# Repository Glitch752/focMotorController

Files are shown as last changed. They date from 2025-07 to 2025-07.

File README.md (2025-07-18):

# FOCMotorController

A 12v brushless DC motor controller capable of [field-oriented control](https://en.wikipedia.org/wiki/Vector_control_(motor)) (also known as vector control), which is a control system concept that can improve the efficiency and power output of motors using current-based feedback.

I wanted to learn how field-oriented control systems (and brushless motor controllers in general) work, so I made a PCB from scratch!

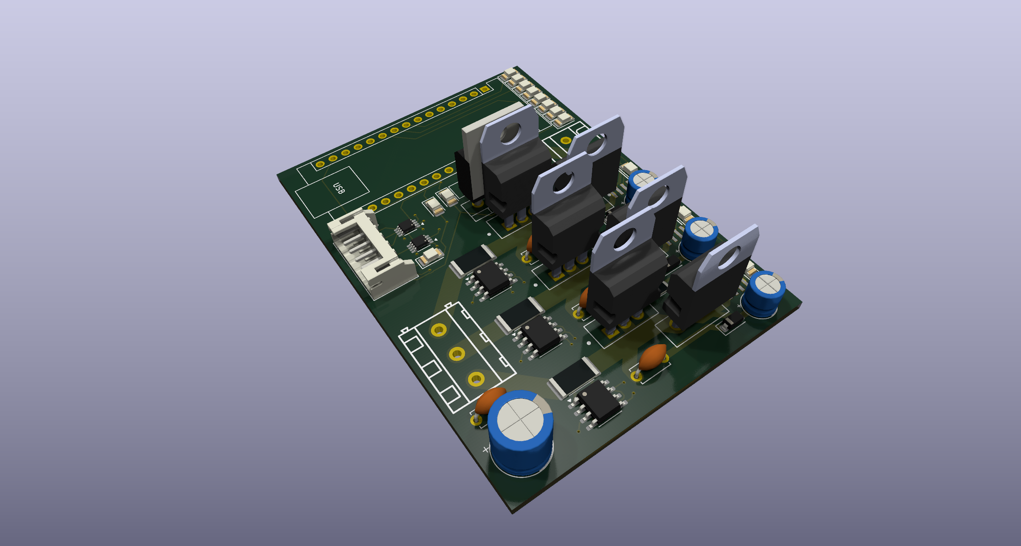
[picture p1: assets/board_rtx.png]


## Design goals
- Allow 30-amp continuous operation
- Run field-oriented control
- Runs off an RP2040 Arduino devboard
- Operate at relatively high efficiency: I don't have a specific goal in mind, but ideally it would experience less than a few watts loss at peak load
- Allow controlling the [REV NEO](https://www.revrobotics.com/rev-21-1650/) series motors from the FRC ecosystem because I have access to many old ones.
- Record accurate quadrature encoder readings for tight closed-loop control
- Build for under $200

## Bill of materials

There are a few main components I needed to choose for this project:
- **MOSFETs:** This is pretty much just a tradeoff between efficiency, size, and price. I landed on the STM [STP55NF06L](https://www.st.com/content/ccc/resource/technical/document/datasheet/49/c5/a8/71/93/60/4f/86/CD00002690.pdf/files/CD00002690.pdf/jcr:content/translations/en.CD000026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) power MOSFET,
which has a very low static resistance when on with a gate voltage of >10V. At only 3.3V, the resistance is quite high, meaning we need a gate driver circuit to improve the driver's efficiency.
- **Gate drivers**: I chose the [IR2104](https://www.infineon.com/dgdl/Infineon-IR2104-DS-v01_00-EN.pdf?fileId=5546d462533600a4015355c7c1c31671) half-bridge gate drivers primarily because they're cheap and widely available.
Also, since they're half-bridge, they manage both the voltage and ground MOSFETs for their phase, which simplifies the control logic.
- **Current measurement circuitry**: There are [quite a few methods available for sensing current](https://www.nxp.com/docs/en/application-note/AN14164.pdf) in motor controllers, but the simplest is using a shunt resistor and relying on Ohm's law.
This is what I ended up doing. I use a [INA240 amplifier](https://www.ti.com/lit/ds/symlink/ina240.pdf) reading across a 6mΩ resistor to convert the tiny voltage potential difference to something readable by the microcontroller.
I'm interested to see what the signal-to-noise ratio will look like.
- Other miscellaneous things like logic level shifters because we're using a 3.3v microcontroller and 5v encoders. All components use a relatively large form-factor where possible to make hand-soldering simpler (altough there are a few tiny SMT components).

Here are all the components required and their price as of July 2025 from JLCPCB.
Of course, many of these can be sourced cheaper elsewhere and soldered manually.

|Name |Purpose|Quantity|JLC part number|Total Price|
|---|---|---|---|---|
|STP55NF06L|The main MOSFET we use|6|[C77582](https://jlcpcb.com/partdetail/STMicroelectronics-STP55NF06L/C77582)|$5.91|
|IR2104STRPBF|The main gate drivers|3|[C2960](https://jlcpcb.com/partdetail/InfineonTechnologies-IR2104STRPBF/C2960)|$1.15|
|Arduino Nano RP2040 Connect|The microcontroller used|1|n/a|$19.10 (on Amazon)|
|SN74LVC2T45DCTR|Level shifters for quadrature encoder input|2|[C22672](https://jlcpcb.com/partdetail/TexasInstruments-SN74LVC2T45DCTR/C22672)|$0.44|
|INA240A1D|The amplifier used for current sensing|3|[C2060769](https://jlcpcb.com/partdetail/TexasInstruments-INA240A1D/C2060769)|$4.32|
|PA2512FKF7W0R006E|The low-resistance 6mΩ shunt resistor|3|[C728340](https://jlcpcb.com/partdetail/YAGEO-PA2512FKF7W0R006E/C728340)|$0.30|
|A16-1000|A resettable fuse for the power input|1|[C135398](https://jlcpcb.com/partdetail/Shenzhen_JDTFuse-A161000/C135398)|$0.09|
|KM477M035F16RR0VH2FP0|470uF capacitor for input smoothing|1|[C47888](https://jlcpcb.com/partdetail/48894-KM477M035F16RR0VH2FP0/C47888)|$0.05|
|KM477M035F16RR0VH2FP0|0.1uF capacitor for input smoothing|1|[C47888](https://jlcpcb.com/partdetail/48894-KM477M035F16RR0VH2FP0/C47888)|$0.05|
|50YXF1MEFC5X11|1uF capacitor for decoupling gate drivers|3|[C2927584](https://jlcpcb.com/partdetail/Rubycon-50YXF1MEFC5X11/C2927584)|$0.13|
|CC1H104MC1FD3F6C10SA|100nF capacitor for bootstrapping|3|[C5375966](https://jlcpcb.com/partdetail/Dersonic-CC1H104MC1FD3F6C10SA/C5375966)|$0.07|
|S6B-PH-K-S(LF)(SN)|6-pin JST connector for encoder|1|[C157920](https://jlcpcb.com/partdetail/JST-S6B_PH_K_S_LF_SN/C157920)|$0.07|
|XL-3216UGC-FB|Green status LEDs|3|[C3646937](https://jlcpcb.com/partdetail/XINGLIGHT-XL_3216UGCFB/C3646937)|$0.04|
|XL-3216SURC-FB|Red power LED|1|[C3646938](https://jlcpcb.com/partdetail/XINGLIGHT-XL_3216SURCFB/C3646938)|$0.01|
|B0530W|500mA diode for bootstrap power|3|[B0530W](https://jlcpcb.com/partdetail/2459-B0530W/C2102)|$0.10|
|MBR1045G|10A Schottky Diode for power source|1|[C79734](https://jlcpcb.com/partdetail/onsemi-MBR1045G/C79734)|$0.86|
|SMAJ15A|TVS diode for voltage spike protection|1|[C113958](https://jlcpcb.com/partdetail/115197-SMAJ15A/C113958)|$0.04|
|WJ128V-5.0-3P|Screw terminal block for phase output|1|[C8270](https://jlcpcb.com/partdetail/Ningbo_KangnexElec-WJ128V_5_03P/C8270)|$0.16|
|WJ128V-5.0-2P|Screw terminal block for voltage input|1|[C8269](https://jlcpcb.com/partdetail/Ningbo_KangnexElec-WJ128V_5_02P/C8269)|$0.11|
|1206W4J0332T5E|3.3kohm resistor, misc|1|[C26041](https://jlcpcb.com/partdetail/26784-1206W4J0332T5E/C26041)|$0.01|
|1206W4F2001T5E|2kohm resistor, misc|1|[C17944](https://jlcpcb.com/partdetail/18632-1206W4F2001T5E/C17944)|$0.01|
|1206W4J0621T5E|620ohm resistor, misc|1|[C25391](https://jlcpcb.com/partdetail/26134-1206W4J0621T5E/C25391)|$0.01|
|FRC1206J101 TS|100ohm resistor, misc|3|[C2907422](https://jlcpcb.com/partdetail/FOJAN-FRC1206J101TS/C2907422)|$0.01|
|1206W4F4702T5E|47kohm pulldown resistors|4|[C25833](https://jlcpcb.com/partdetail/26576-1206W4F4702T5E/C25833)|$0.02|
|FRC1206F19R6TS|19.6ohm gate resistors|6|[C2933621](https://jlcpcb.com/partdetail/FOJAN-FRC1206F19R6TS/C2933621)|$0.02|

Total part cost for 1 board:
- $8.02 without microcontroller or MOSFETs
- $13.93 without microcontroller
- $33.03 with microcontroller   

Note that, if you're doing assembly through something like JLCPCB, you'll need to make 5. If you don't need 5 boards, you can avoid assembly for the MOSFETs and order them yourself. They're one of the easiest components to solder on the board.

## FOC writeup
Here, I'll document my current knowledge of field oriented control for my own reference and to see what I need to look further into. Please note all this information may not be correct since BLDC control is still a new subject to me.

Field oriented control is a mechanism to control brushless DC motors that guarantees torque will always be applied directly perpendicular to the motor. It increases the efficiency, maximum speed, and power output of controlled motors. However, it's also relatively expensive to calculate and suffers from MOSFET switching losses because we must use PWM control to generate an effective sine wave.

### Definitions and acronyms
- **Motor**: A device that converts electrical energy into mechanical energy. Motors typically use moving permanent magnets and fixed electromagnets to generate a magnetic field that causes the rotor to spin.
  - **Winding**: A coil of wire that generates a magnetic field when current flows through it.
  - **Inductor**: Another name for a winding, typically used in the context of inductors that store energy in a magnetic field.
  - **Phase**: A set of windings in a motor that is independently controlled. Brushless motors typically have three phases, which are often referred to as A, B, and C or U, V, and W.
  - **Rotor**: The *rot*ating part of the motor containing permanent magnets. This is the part that spins.
    - **Poles**: The number of permanent magnets attached to the rotor. This isn't necessarily a multiple of the number of phases, but should be a multiple of 2 (since two identical magnet poles can't be beside each other).
  - **Stator**: The *stat*ionary part of the motor containing the windings. This is the part that generates the magnetic field. In a 3-phase motor, the stator has 3 sets of windings, each 120 electric degrees apart.
    - **Slots**: The number of coils on the stator. Motors will have a number of slots that is a multiple of the number of phases.
  - **BLDC**: Brushless DC. Brushed motors have physical contacts that dictate when phases are activated, while brushless motors rely on electrical signals to control the phases. Brushless motors can be faster, more reliable, and more efficient, but this comes at the cost of complexity.[<sup>1</sup>](#footnote-1)
  - **PMSM**: Permanent Magnet Synchronous Motors. The uses of this term are somewhat murky and confused with BLDC, so I will refrain from using it to avoid confusion.[<sup>2</sup>](#footnote-2)
  - **Mechanical angle**: The physical angle of the rotor in the motor; 1 revolution of the rotor is 360 degrees. The mechanical angle is used for position and speed feedback.
  - **Electrical angle**: The electrical angle describes the position of the rotor relative to the stator's magnetic field. It cycles faster than the mechanical angle by a factor equal to the number of pole pairs. The electrical angle is used for control calculations (e.g. it's the angle used in park and clarke transformations; see below).
- **FOC**: Field-oriented control, a method of controlling brushless motors that uses current-based feedback to apply torque directly perpendicular to the rotor.
- **Inverter**: Components that convert DC power to AC power. In our case, the circuitry that converts the motor controller's input voltage to phase voltages.
  - **MOSFET**: Metal-Oxide-Semiconductor Field-Effect Transistor; a particular type of transistor that can effectively act as a switch when appropriate signals are applied. 6 MOSFETs are used for BLDC motor control: one for ground and one for voltage of each phase.
  - **Gate driver / FET driver**: A circuit that controls MOSFETs, providing the necessary voltage while decoupling the microcontroller from the relatively high current draw of switching MOSFETs.
  - **Half bridge**: A circuit that controls two MOSFETs to switch a phase between voltage and ground. Half bridges are used for each phase in BLDC motor control.
- **Encoder**: A device that measures the position of the rotor relative to the stator. Accurate position measurement is crucial for FOC so we know where to apply torque.
  - **Hall effect sensor**: A type of sensor that detects magnetic fields.
  - **Quadrature encoder**: A type of encoder that uses two signals to determine the position of the rotor. It can detect both position and direction of rotation. Quadrature encoders can use hall sensors, optical sensors, or other methods.
    - **A/B channels**: Quadrature encoders have two primary outputs, A and B, which are 90 degrees out of phase. This communicates both velocity and direction of rotation.
    - **C channel / index**: Some quadrature encoders (including those we rely on) have a third channel, C, which indicates a specific position of the rotor. This is used for homing the rotor to find its initial position.
- **PWM**: Pulse-width modulation. A method of controlling the amount of power delivered by quicking switching something on and off.
  - **Duty cycle**: The percentage of time that a signal is on compared to the total time. For example, a 25% duty cycle means the signal is on for 25% of the time and off for 75% of the time.
  - **SVM**: Space vector modulation. An algorithm for effectively creating AC waveforms through PWM signals. SVM is commonly used for BLDC motor control because it reduces noise and vibration compared to more naive approaches.
- **Driving frequency**: Generally, the frequency of PWM pulses sent to the half bridge drivers. A higher driving frequency creates a smoother output signal but requires faster and more expensive hardware. Generally in the range of 20 to 80 kHz.
- **Control frequency**: The frequency of the control system driving the output voltages. Control systems generally operate around 1 to 5 kHz.
- **Inrunner/outrunner**: Two types of brushless motors that differ in how the stator and rotor are arranged.
  - **Inrunner**: The rotor is inside the stator, which typically contains large windings pointing inward. Inrunner motors generally have a higher maximum speed and efficiency.
  - **Outrunner**: The rotor is outside the stator, which typically contains smaller windings pointing outward. In some cases, this means the rotor is the outer body of the motor. In outrunner motors, the rotor is sometimes also called a can. Outrunner motors generally have a higher torque output.
- **Flux**: Shorthand for magnetic flux linkage. Magnetic flux linkage can be thought of as the "magnetic field strength" in the motor. For PMSM control, our reference flux is 0 (but we still need to control it to keep it there).
- There are many coordinate systems used for BLDC control; see [figure 1](#figure-1-a-diagram-of-coordinate-systems-used-in-foc). Here are the most important ones and their common names:
  - **Stator X axis / alpha**: The "horizontal" (on a side profile) axis of the motor stator.
  - **Stator Y axis / beta**: The "vertical" (on a side profile) axis of the motor stator.
  - **Winding U, V, and W axes**: The axes pointing outwards for the three phases of the motor, 120 degrees offset from each other. Axis U is typically aligned with the stator X axis.
  - **Rotor direct axis / d**: The axis of the rotor that is parallel to the rotor's magnetic field that generates flux.
  - **Rotor quadrature axis / q**: The axis of the rotor that is perpendicular to the rotor's magnetic field that generates torque.
- **Electromotive force / back EMF**: The voltage generated by the motor itself while spinning.[<sup>3</sup>](#footnote-3)
- Transformations are used in motor control to make manipulating the signals simpler.
  - **Clarke transformation**: Also known as the alpha-beta transformation; converts the three-phase stator currents u, v, and w into stator axes alpha and beta.
  - **Park transformation**: Also known as the direct-quadrature-zero transformation; converts stator-aligned components into rotor axes q and d with respect to the motor's rotating magnetic field.
- **Proportional-integral (PI) controller**: A feedback-based control mechanism to regulate processes that require dynamic adjustment or can't be precisely modelled mathematically. PI controllers are used to regulate rotor axis (q and d) currents by controlling the maximum PWM duty cycle for each phase.[<sup>4</sup>](#footnote-4)

### FOC process

The broad overview of FOC control is as follows:
1. Gather the measured position of the rotor using the encoder.
2. Transform phases into the rotor coordinate system.
3. Calculate the required current in the rotor quadrature axis (q) to generate the desired torque.
4. Calculate the required current in the rotor direct axis (d) to generate the desired magnetic field.
5. Transform the rotor coordinate system back to the phases' coordinate systems.
6. Calculate the required voltage to apply to each phase to generate the desired current.
7. Apply the calculated voltage to each phase using PWM.
8. Repeat at a high frequency.

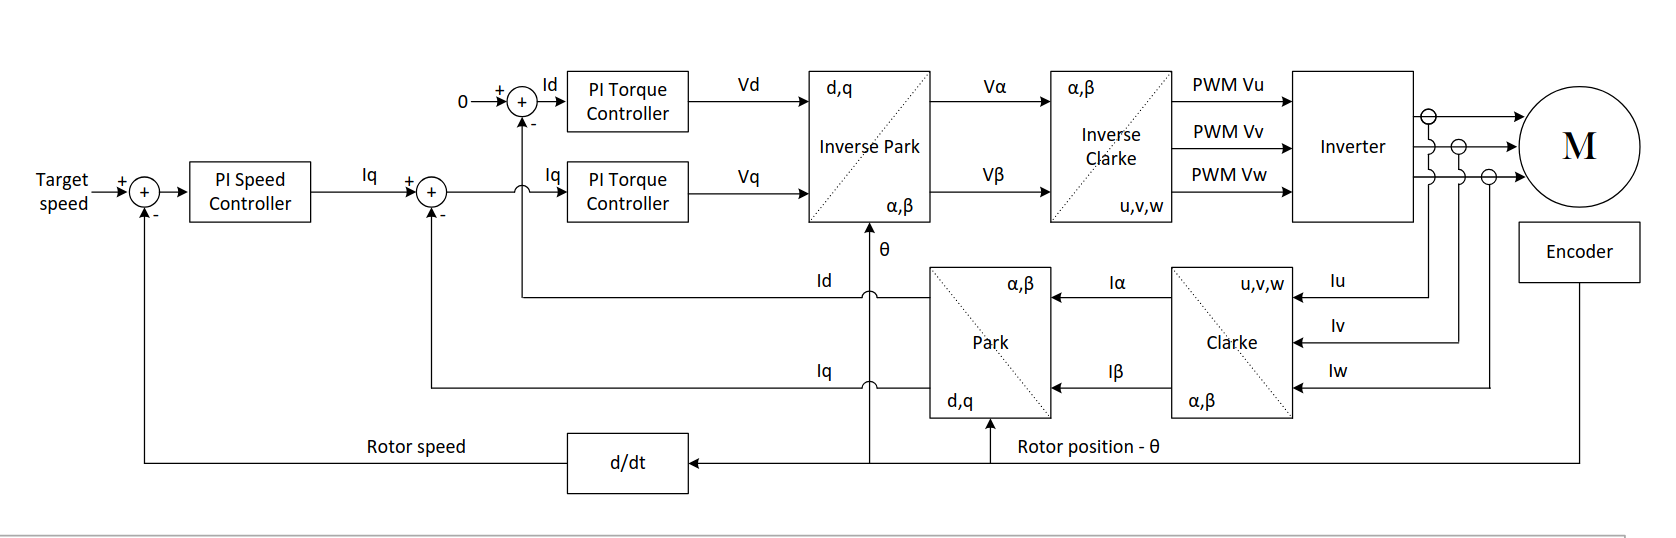
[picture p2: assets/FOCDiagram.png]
FOC diagram showing the above process

From [this great presentation](https://www.ti.com/lit/ml/slyp711/slyp711.pdf).  

There are a few important things to note:
- We can't track the encoder position fast enough to respond accurately to the rotor position at high speeds,
  so we must perform latency compensation of some sort.
- The current in the rotor direct axis (d) is typically set to zero, meaning we only control the rotor quadrature axis (q).
  This is because the d-axis current doesn't generate torque, so we don't care about it for most applications.
- This doesn't account for current limiting, which is a whole separate topic that I honestly
  don't understand very well. Currently, I naively clamp the applied current to a maximum value.

### Footnotes

<h4 id="footnote-1"><sup>1</sup> "Brushless DC"</h4>
Confusingly, "brushless DC motor control" is often used to refer to brushless motors that are controlled with DC voltage through a motor controller, even though the motor itself is an AC motor. This is because the motor controller generates a sine wave using PWM signals, which is then applied to the motor phases.

<h4 id="footnote-2"><sup>2</sup> "Permanent Magnet Synchronous Motors. The uses of this term are somewhat murky and confused with BLDC [...]"</h4>
Technically, brushless motors can also be switched reluctance motors or induction motors (also known as asynchronous motors). However, the majority of brushless DC motors are PMSM. Synchronous motors are a subset of brushless motors whose speed is independent of the load.

<h4 id="footnote-3"><sup>3</sup> "Back EMF is the voltage generated by the motor itself while spinning"</h4>
When brushless motors spin, the rotor generates current in the stator that opposes the applied voltage. Back EMF is linearly proportional to the rotational speed of the motor, so it's one of the forces that limits brushless motors' maximum speed.  
Back EMF is sometimes used to determine the position and speed of brushless motors in sensorless control, but almost never for FOC because it's not precise enough. It can also be used to our advantage for "braking", which entails shorting the phases together to make the motor resist rotation.  
  
<h4 id="footnote-4"><sup>4</sup> "PI controllers are a feedback-based control mechanism [...]"</h4>
PI controllers take the error between the current and desired state as an input and adjust the output based on the error. They have two components (hence the name): a proportional component that linearly adjusts the output based on the error, and an integral component that accumulates error over time. The two components are added to get the final output.  
PI controllers are a subset of the more general PID controllers, which also include a derivative component that predicts future error based on the rate of change of the error. In a PI controller, the components serve different purposes; the proportional component provides immediate response to error, while the integral component helps eliminate steady-state error by adjusting the output based on accumulated error over time.  

### Figures
#### Figure 1: A diagram of coordinate systems used in FOC
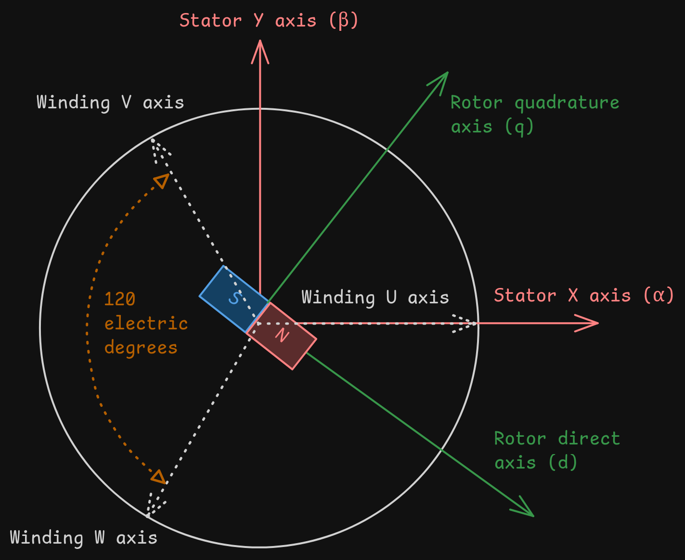
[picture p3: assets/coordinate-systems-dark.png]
A graphical explanation of stator, rotor, and winding motor coordinate systems


## Software
Currently, there's a testing piece of software written in Python to run on a local system and simulate the motor controller.
Obviously, Python won't be fast enough for high-speed closed-loop control on the motor controller,
so I'll move to C++ once I have the ability to test more easily.

## Hackatime
Project name: `focMotorController`



Note that I initially had some issues with kicad-wakatime, so it didn't track ~8 hours of work :(

## Future investigation (once I actually have a PCB lol)
- Does it actually work?
- Do we need a heatsink? We should be dissipating an average of ~0.32W per MOSFET at peak load, and 2 watts spread over 6 devices is a very minimal amount of heat. Maybe if we drive it harder, but the rest of the circuit would probably break before the MOSFETs...
- There's an interesting new-ish algorithm seen primarily in acadamia called [Deadbeat Direct Torque and Flux Control](https://www.mdpi.com/1996-1073/15/9/3009); how difficult would it be to implement this?
- Understand and determine the advantages of [discontinuous PWM](https://imperix.com/doc/implementation/discontinuous-pwm) signaling

### Future investigation for the PCB
- Should we have separate enable lines per half bridge?
- Is there a more efficient and accurate, yet inexpensive, way to measure current?
- How can I minimize signal noise in a board carrying high current?
- How can I improve the gate driver circuitry to minimize switching losses?
- Should we instead use full half bridge chips instead of drivers and MOSFETs?

## Resources
- [Current Sensing Techniques in Motor Control Applications - NXP](https://www.nxp.com/docs/en/application-note/AN14164.pdf)
- [Bootstrap Circuitry Selection for Half Bridge Configurations - Texas Instruments](https://www.ti.com/lit/an/slua887a/slua887a.pdf)
- [Bypass Capacitor, Its Functions and Applications - Elprocus](https://www.elprocus.com/bypass-capacitor-its-functions-and-applications/)
- [How to Make Advanced BLDC Motor Controllers - Altium](https://resources.altium.com/p/build-advanced-brushless-motor-controller)
- [Field-Oriented Control (FOC) for BLDC Motors: A Beginner’s Guide - Mechtex](https://mechtex.com/blog/field-oriented-control-foc-for-bldc-motors-a-beginners-guide)
- [Discontinuous PWM (DPWM) - Imperix](https://imperix.com/doc/implementation/discontinuous-pwm)
- [Proportional–integral–derivative controller](https://en.wikipedia.org/wiki/Proportional%E2%80%93integral%E2%80%93derivative_controller)
- [Space vector modulation - Wikipedia](https://en.wikipedia.org/wiki/Space_vector_modulation)
- [Space Vector PWM Intro - Switchcraft](https://www.switchcraft.org/learning/2017/3/15/space-vector-pwm-intro) (has great animations)
- [Protect Your BLDC Motor Drive with Cycle-by-cycle Current Limit Control - Texas Instruments](https://www.ti.com/lit/ta/ssztbp2/ssztbp2.pdf)
- [PMSM Control with DSCs and MCUs - Microchip](https://www.microchip.com/en-us/solutions/technologies/motor-control-and-drive/motor-types/permanent-magnet-synchronous-motors)
- [Vector control (motor) - Wikipedia](https://en.wikipedia.org/wiki/Vector_control_(motor))
- [Demystifying BLDC motor commutation - Texas Instruments](https://www.ti.com/lit/ml/slyp711/slyp711.pdf)
- [Alpha–beta transformation - Wikipedia](https://en.wikipedia.org/wiki/Alpha%E2%80%93beta_transformation)
- [Direct-quadrature-zero transformation - Wikipedia](https://en.wikipedia.org/wiki/Direct-quadrature-zero_transformation)
- [Field Oriented Control (FOC) - A Deep Dive - Performance Motion Devices](https://www.pmdcorp.com/resources/type/articles/get/field-oriented-control-foc-a-deep-dive-article)
- [fasaxc/pico-bldc - Github](https://github.com/fasaxc/pico-bldc/tree/main)

### Datasheets
- [INA240 Bidirectional, Ultra-Precise Current Sense Amplifier](https://www.ti.com/lit/ds/symlink/ina240.pdf)
- [Datasheet IR2104(S) & (PbF)](https://www.infineon.com/dgdl/Infineon-IR2104-DS-v01_00-EN.pdf?fileId=5546d462533600a4015355c7c1c31671)
- [Datasheet STP55NF06L N-channel Power MOSFET](https://www.st.com/content/ccc/resource/technical/document/datasheet/49/c5/a8/71/93/60/4f/86/CD00002690.pdf/files/CD00002690.pdf/jcr:content/translations/en.CD000026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)

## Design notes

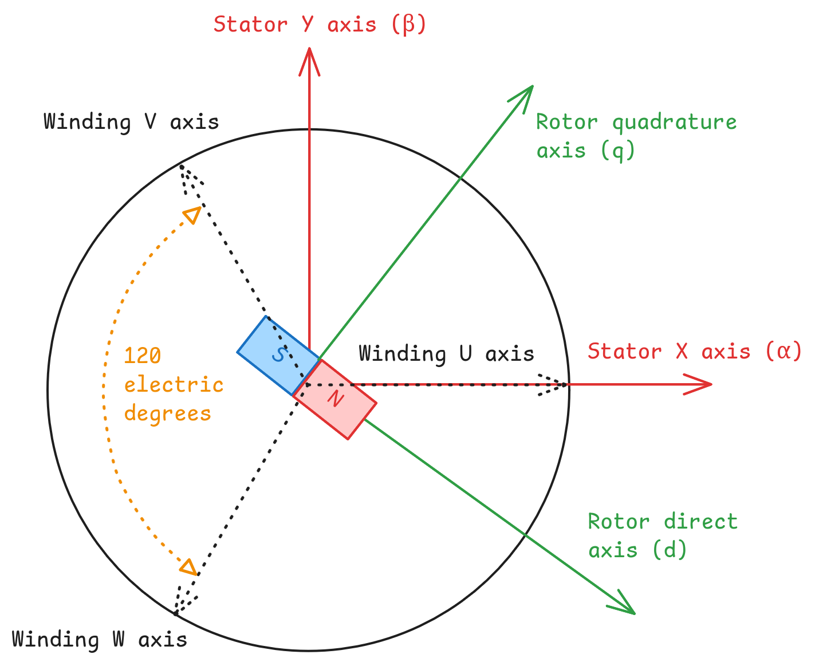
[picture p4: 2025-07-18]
assets/coordinate-systems.png

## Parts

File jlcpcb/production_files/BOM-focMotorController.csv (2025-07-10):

Comment | Designator | Footprint | LCSC | Quantity
SMAJ15A - TVS diode for voltage spike protection | D1 | D_SMA | C113958 | 1
Resettable polyfuse for overcurrent protection | F1 | A16-1000 | C135398 | 1
JST-PH encoder connection | J2 | JST_PH_S6B-PH-K_1x06_P2.00mm_Horizontal | C157920 | 1
2k | R2 | R_1206_3216Metric | C17944 | 1
Amplifier A | U12,U13,U14 | SOIC-8_3.9x4.9mm_P1.27mm | C2060769 | 3
Bootstrap charger | D7,D8,D9 | D_SOD-123 | C2102 | 3
74LVC2T45DC | U1,U2 | VSSOP-8_2.3x2mm_P0.5mm | C22672 | 2
620ohm | R3 | R_1206_3216Metric | C25391 | 1
Pulldown 47k | R11,R13,R7,R8 | R_1206_3216Metric | C25833 | 4
3.3k | R1 | R_1206_3216Metric | C26041 | 1
100ohm | R4,R5,R6 | R_1206_3216Metric | C2907422 | 3
Decoupling B 1uF/25V | C6,C7,C8 | CP_Radial_D5.0mm_P2.00mm | C2927584 | 3
Gate BL 19.6ohm | R10,R12,R19,R20,R22,R9 | R_1206_3216Metric | C2933621 | 6
IR2104 Gate Driver B | U10,U11,U9 | IR2104SPBF | C2960 | 3
Status LED 1 (green) | D4,D5,D6 | LED_1206_3216Metric | C3646937 | 3
Power LED (red) | D3 | LED_1206_3216Metric | C3646938 | 1
0.1uF ceramic | C2 | C_Disc_D5.0mm_W2.5mm_P5.00mm | C400087 | 1
470uF electrolytic | C1 | CP_Radial_D8.0mm_P3.50mm | C47888 | 1
Bootstrap A 0.1uF/25v | C3,C4,C5 | C_Disc_D5.0mm_W2.5mm_P5.00mm | C5375966 | 3
Shunt A 6uohm | R14,R15,R16 | R_2512_6332Metric | C728340 | 3
MOSFET A low | U3,U4,U5,U6,U7,U8 | STP55NF06L | C77582 | 6
MBR1045G | D2 | TO-220-2_Vertical | C79734 | 1
Power input | P2 | WJ128V-5.0-2P | C8269 | 1
WJ128V-5.0-3P | P1 | WJ128V-5.0-3P | C8270 | 1

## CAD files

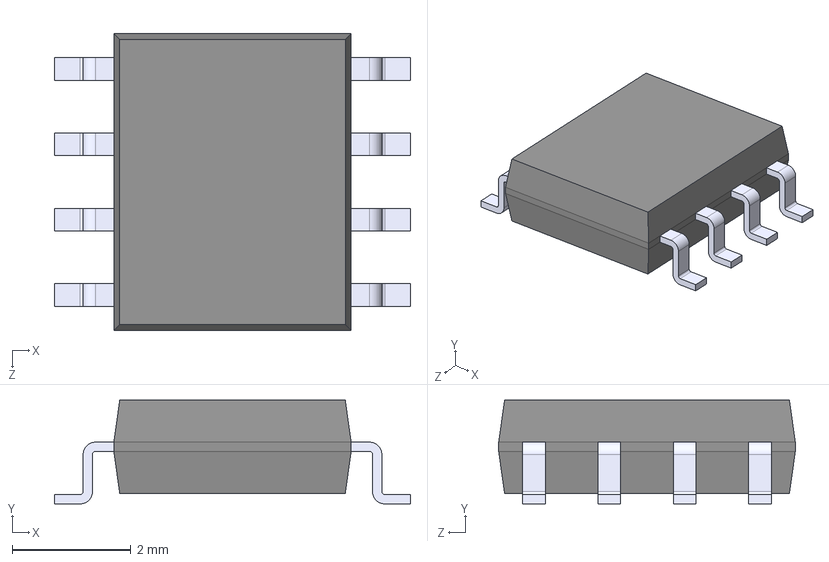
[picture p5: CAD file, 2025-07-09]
footprints/IR2104SPBF.step
6.00 x 1.75 x 5.00 mm

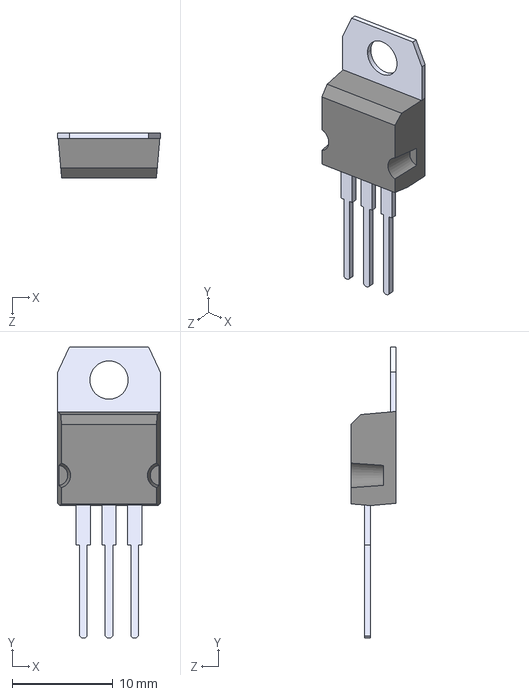
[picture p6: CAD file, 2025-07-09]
footprints/STP55NF06L.step
10.2 x 28.9 x 4.50 mm

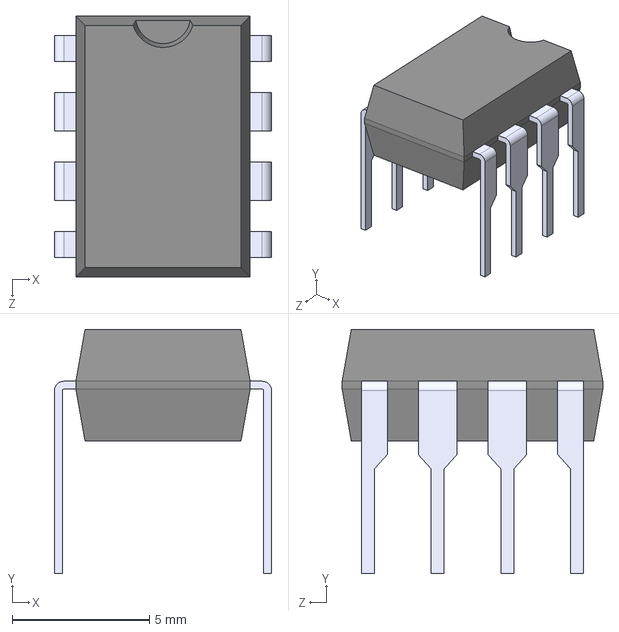
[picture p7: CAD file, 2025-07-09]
footprints/TC4420EPA.step
7.91 x 8.89 x 9.50 mm

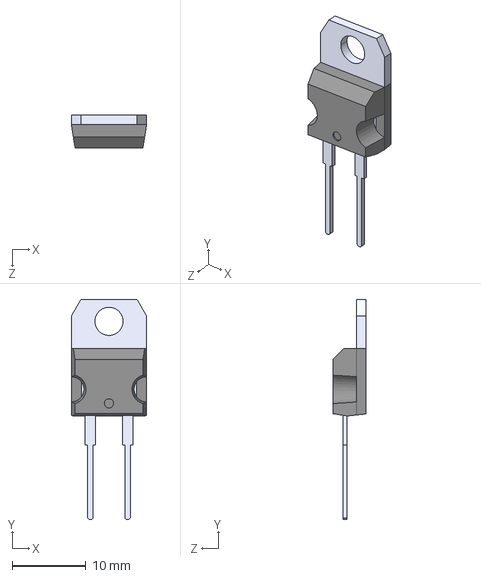
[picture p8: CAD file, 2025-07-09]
footprints/STPS20L15D.step
10.2 x 29.8 x 4.50 mm

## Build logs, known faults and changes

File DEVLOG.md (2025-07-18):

# Small devlog

Total time spent so far: ~19 hours (~11 tracked by hackatime)

## Initial research
Time taken: ~2 hours

I determined the appropriate MOSFETs and circuitry required for field-oriented control.

## Initial PCB
Time taken: ~8 hours

I made the schematic and PCB layout in KiCad for the bare-minimum driver circuitry required for FOC. There were a few flaws with my initial design, like measuring current on the low MOSFET source, which I learned isn't sufficient for field-oriented control.

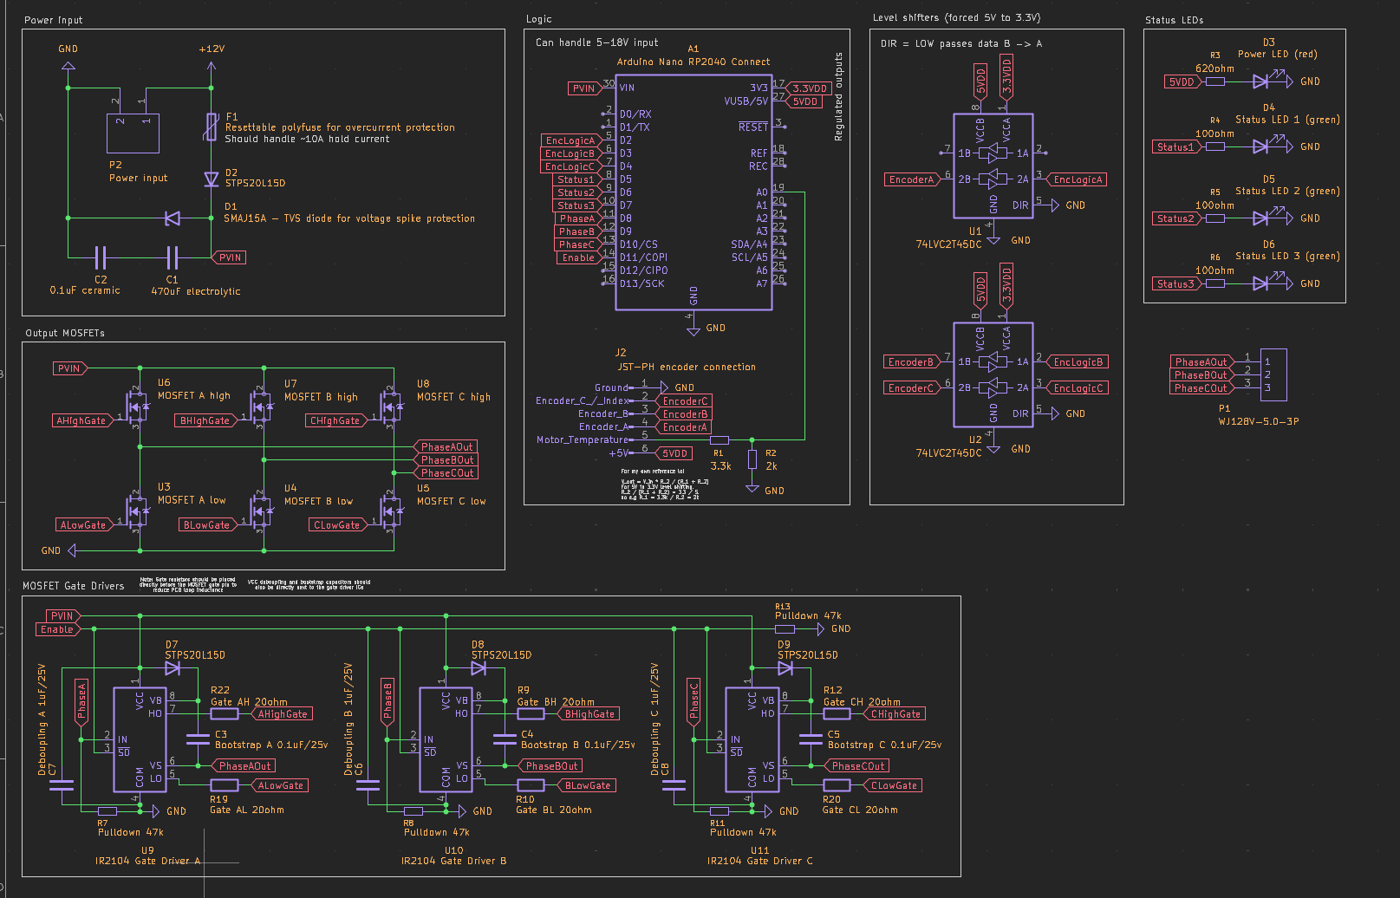
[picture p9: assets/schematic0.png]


## Iterating on the PCB
Time taken: ~3 hours

I iterated on the design to make the PCB much more compact and clean. I'm not yet aware of any issues with the new version of the PCB, so next up is software.

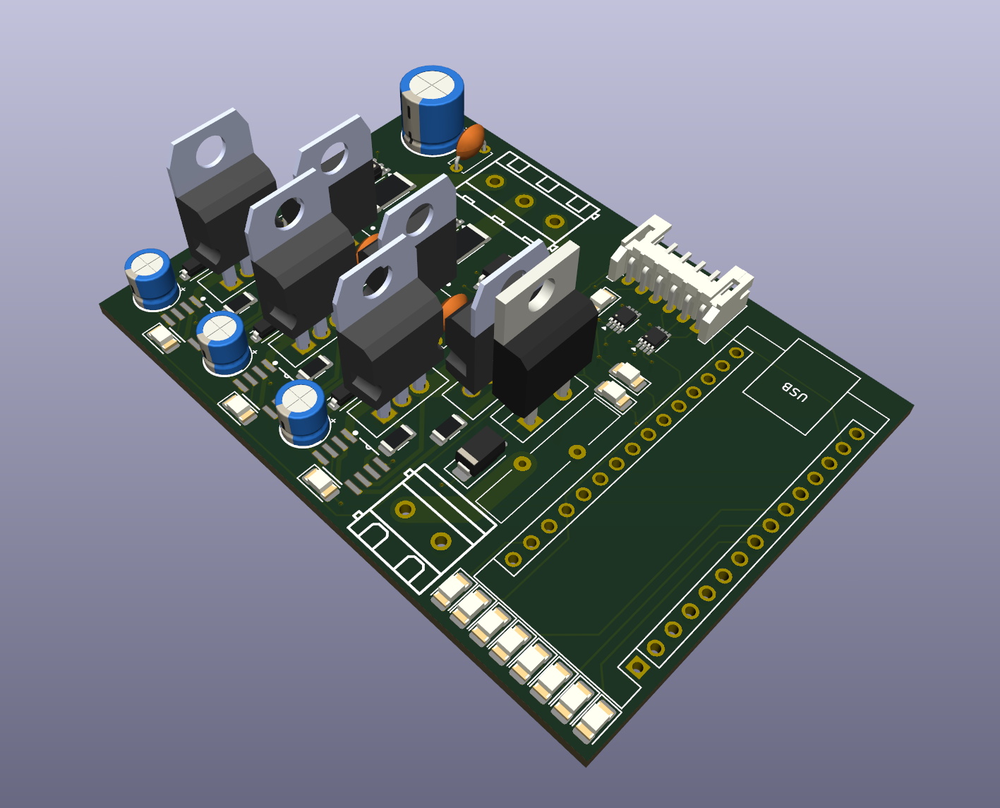
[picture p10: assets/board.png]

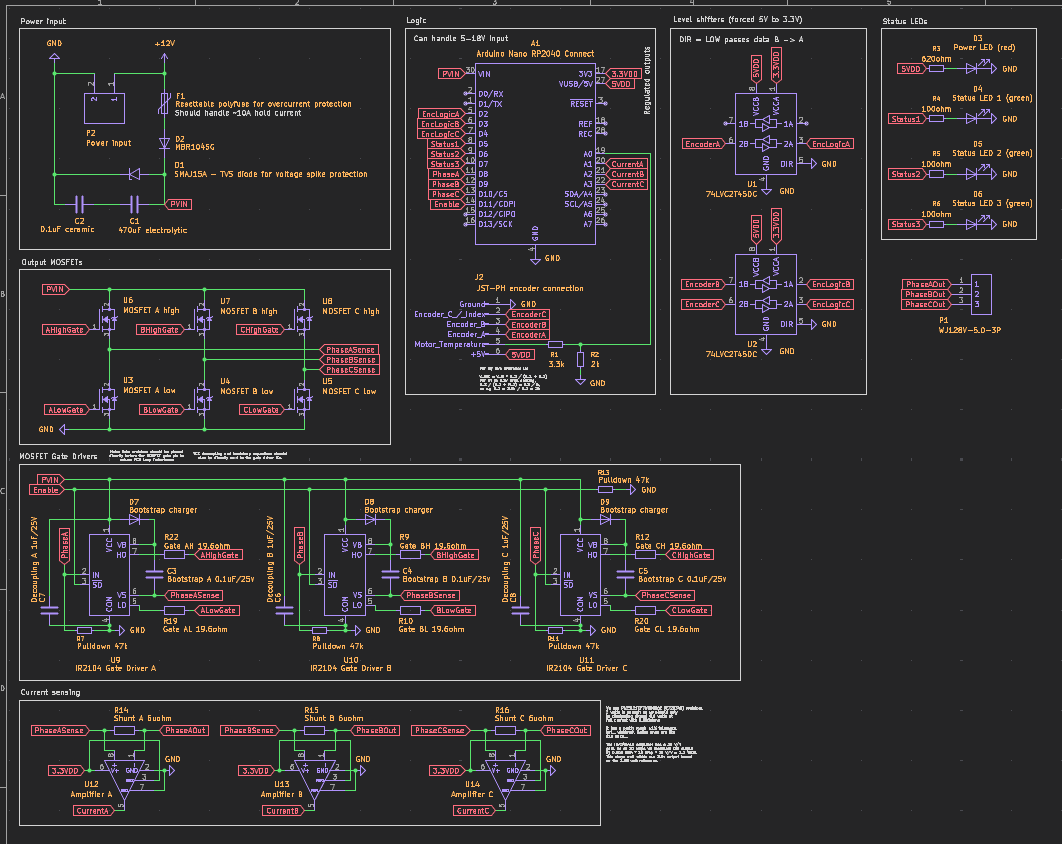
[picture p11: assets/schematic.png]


## Improve documentation
Time taken: ~30 minutes

I improved the [documentation of the project](https://github.com/Glitch752/focMotorController/blob/472c54bfc41076d94987bcc05ba8eb1525c3219e/README.md).

## Start implementing basic controller simulator in Python
Time taken: ~3 hours

I learned about some of the operating principles of FOC and started implementing a simulator. It's currently _very_ broken and incomplete (and doesn't even simulate phases separately), but I'm slowly improving it.

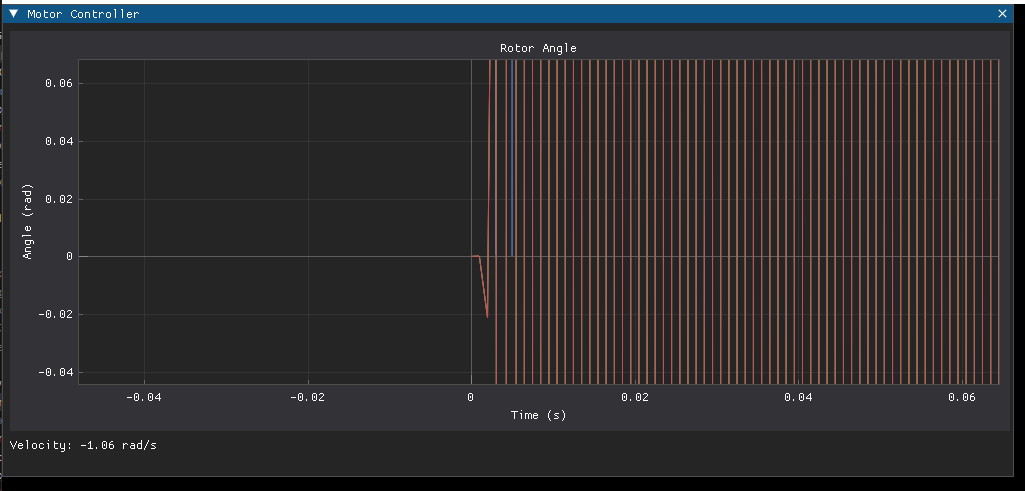
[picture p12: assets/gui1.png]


## Start preparing PCB for JLCPCB
Time taken: ~1 hour

I started preparing the PCB to be manufactured with the excellent [kicad-jlcpcb-tools](https://github.com/Bouni/kicad-jlcpcb-tools) plugin.

## Finish JLCPCB part assignments and create/check exhaustive BOM
Time taken: ~1 hour

## Start FOC writeup
Time taken: ~2 hours

I created an initial writeup of my understanding of field oriented control in the readme.

## Vastly improve motor simulation
Time taken: ~7 hours

The FOC simulaton now sort of, kind of, maybe works!  
At least, we're able to command the motor to slowly spin and move it a bit. The phase outputs look somewhat sinusoidal as well.  
The FOC part itself needs more work, but the motor simulation is certainly better now.

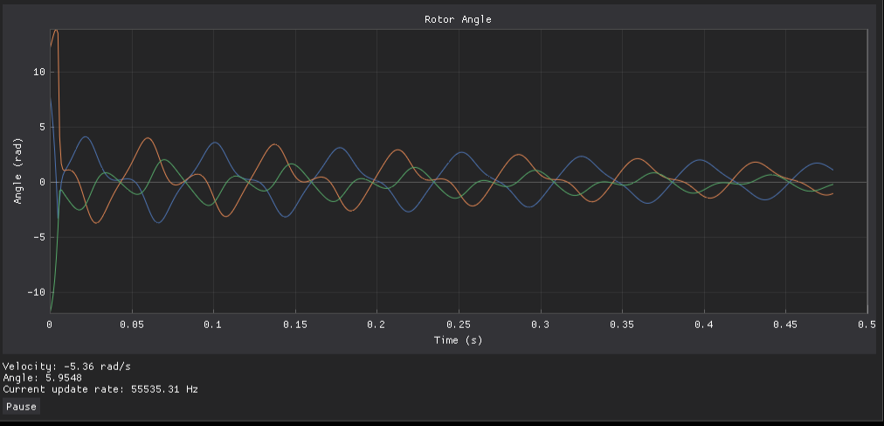
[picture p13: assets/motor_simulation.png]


## Improve FOC control and simulator GUI
Time taken: ~5 hours

The simulator is a lot more usable now, and I also implemented a six-step controller as point of comparison for FOC.  
I think the FOC control could still use some work, but it is now stable and works relatively well.  

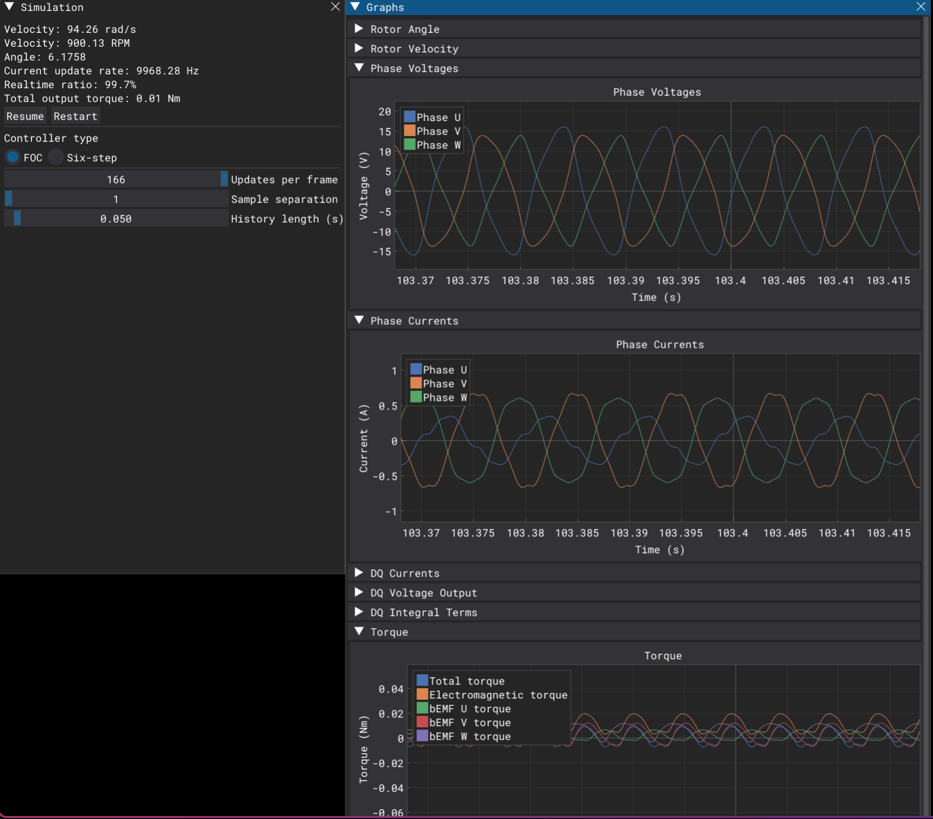
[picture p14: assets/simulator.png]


## Small PCB fixes and updates
Time taken: ~2 hours

I adjusted the PCB to use copper pours for high current traces and opened areas on the mask for solder if needed.

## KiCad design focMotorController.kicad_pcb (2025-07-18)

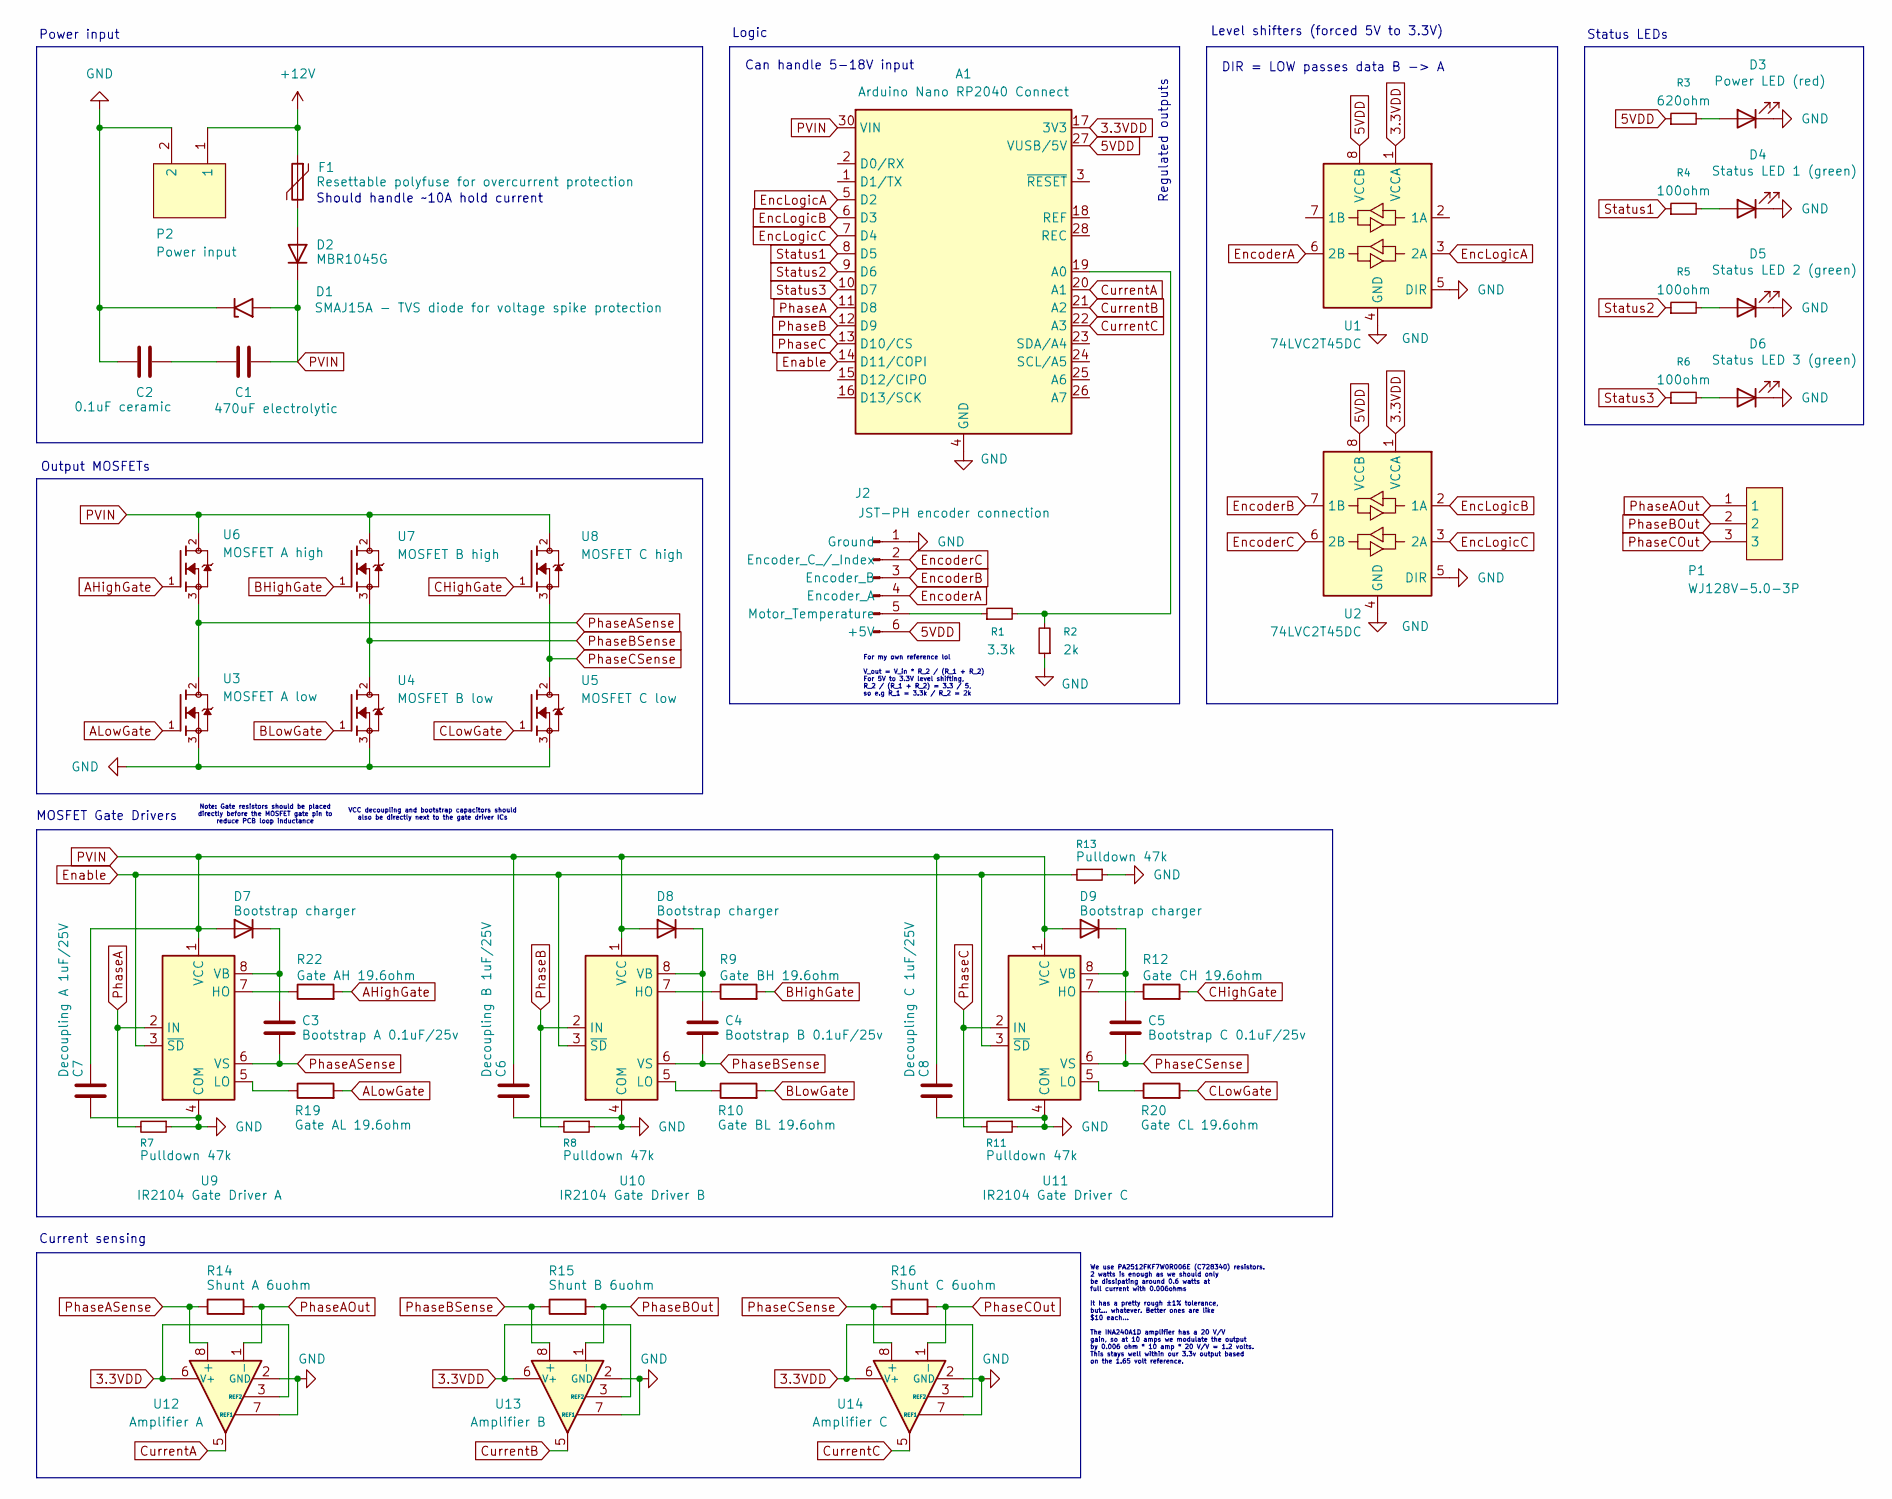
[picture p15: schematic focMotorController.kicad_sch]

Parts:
A1: Arduino Nano RP2040 Connect; Arduino_Nano
C1: 470uF electrolytic; CP_Radial_D8.0mm_P3.50mm
C2: 0.1uF ceramic; C_Disc_D5.0mm_W2.5mm_P5.00mm
C3: Bootstrap A 0.1uF/25v; C_Disc_D5.0mm_W2.5mm_P5.00mm
C4: Bootstrap B 0.1uF/25v; C_Disc_D5.0mm_W2.5mm_P5.00mm
C5: Bootstrap C 0.1uF/25v; C_Disc_D5.0mm_W2.5mm_P5.00mm
C6: Decoupling B 1uF/25V; CP_Radial_D5.0mm_P2.00mm
C7: Decoupling A 1uF/25V; CP_Radial_D5.0mm_P2.00mm
C8: Decoupling C 1uF/25V; CP_Radial_D5.0mm_P2.00mm
D1: SMAJ15A - TVS diode for voltage spike protection; D_SMA
D2: MBR1045G; TO-220-2_Vertical
D3: Power LED (red); LED_1206_3216Metric
D4: Status LED 1 (green); LED_1206_3216Metric
D5: Status LED 2 (green); LED_1206_3216Metric
D6: Status LED 3 (green); LED_1206_3216Metric
D7, D8, D9: Bootstrap charger; D_SOD-123
F1: Resettable polyfuse for overcurrent protection; A16-1000
J2: JST-PH encoder connection; JST_PH_S6B-PH-K_1x06_P2.00mm_Horizontal
P1: WJ128V-5.0-3P; LCSC Part C8270
P2: Power input; WJ128V-5.0-2P; LCSC Part C8269
R1: 3.3k; R_1206_3216Metric
R2: 2k; R_1206_3216Metric
R3: 620ohm; R_1206_3216Metric
R4, R5, R6: 100ohm; R_1206_3216Metric
R7, R8, R11, R13: Pulldown 47k; R_1206_3216Metric
R9: Gate BH 19.6ohm; R_1206_3216Metric
R10: Gate BL 19.6ohm; R_1206_3216Metric
R12: Gate CH 19.6ohm; R_1206_3216Metric
R14: Shunt A 6uohm; R_2512_6332Metric
R15: Shunt B 6uohm; R_2512_6332Metric
R16: Shunt C 6uohm; R_2512_6332Metric
R19: Gate AL 19.6ohm; R_1206_3216Metric
R20: Gate CL 19.6ohm; R_1206_3216Metric
R22: Gate AH 19.6ohm; R_1206_3216Metric
U1, U2: 74LVC2T45DC; VSSOP-8_2.3x2mm_P0.5mm
U3: MOSFET A low; STP55NF06L
U4: MOSFET B low; STP55NF06L
U5: MOSFET C low; STP55NF06L
U6: MOSFET A high; STP55NF06L
U7: MOSFET B high; STP55NF06L
U8: MOSFET C high; STP55NF06L
U9: IR2104 Gate Driver A; IR2104SPBF
U10: IR2104 Gate Driver B; IR2104SPBF
U11: IR2104 Gate Driver C; IR2104SPBF
U12: Amplifier A; SOIC-8_3.9x4.9mm_P1.27mm
U13: Amplifier B; SOIC-8_3.9x4.9mm_P1.27mm
U14: Amplifier C; SOIC-8_3.9x4.9mm_P1.27mm

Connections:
3.3VDD: A1.17 (3V3), U1.1 (VCCA), U2.1 (VCCA), U12.3 (REF2), U12.6 (V+), U13.3 (REF2), U13.6 (V+), U14.3 (REF2), U14.6 (V+)
5VDD: A1.27 (VUSB/5V), J2.6 (+5V), R3.1, U1.8 (VCCB), U2.8 (VCCB)
+12V: F1.1, P2.1
AHighGate: R22.2, U6.1
ALowGate: R19.2, U3.1
BHighGate: R9.2, U7.1
BLowGate: R10.2, U4.1
CHighGate: R12.2, U8.1
CLowGate: R20.2, U5.1
CurrentA: A1.20 (A1), U12.5
CurrentB: A1.21 (A2), U13.5
CurrentC: A1.22 (A3), U14.5
Enable: A1.14 (D11/COPI), R13.2, U9.3 (~SD), U10.3 (~SD), U11.3 (~SD)
EncLogicA: A1.5 (D2), U1.3 (2A)
EncLogicB: A1.6 (D3), U2.2 (1A)
EncLogicC: A1.7 (D4), U2.3 (2A)
EncoderA: J2.4 (Encoder_A), U1.6 (2B)
EncoderB: J2.3 (Encoder_B), U2.7 (1B)
EncoderC: J2.2 (Encoder_C_/_Index), U2.6 (2B)
GND: A1.4 (GND), A1.29 (GND), C2.1, C6.2, C7.2, C8.2, D1.1 (A1), D3.1 (K), D4.1 (K), D5.1 (K), D6.1 (K), J2.1 (Ground), P2.2, R2.1, R7.1, R8.1, R11.1, R13.1, U1.4 (GND), U1.5 (DIR), U2.4 (GND), U2.5 (DIR), U3.3, U4.3, U5.3, U9.4 (COM), U10.4 (COM), U11.4 (COM), U12.2 (GND), U12.4 (GND), U12.7 (REF1), U13.2 (GND), U13.4 (GND), U13.7 (REF1), U14.2 (GND), U14.4 (GND), U14.7 (REF1)
unnamed: A1.19 (A0), R1.2, R2.2
unnamed: C1.1, C2.2
unnamed: D2.2 (A), F1.2
unnamed: D3.2 (A), R3.2
unnamed: D4.2 (A), R4.2
unnamed: D5.2 (A), R5.2
unnamed: D6.2 (A), R6.2
unnamed: C3.1, D7.1 (K), U9.8 (VB)
unnamed: C4.1, D8.1 (K), U10.8 (VB)
unnamed: C5.1, D9.1 (K), U11.8 (VB)
unnamed: J2.5 (Motor_Temperature), R1.1
unnamed: R22.1, U9.7 (HO)
unnamed: R19.1, U9.5 (LO)
unnamed: R9.1, U10.7 (HO)
unnamed: R10.1, U10.5 (LO)
unnamed: R12.1, U11.7 (HO)
unnamed: R20.1, U11.5 (LO)
PVIN: A1.30 (VIN), C1.2, C6.1, C7.1, C8.1, D1.2 (A2), D2.1 (K), D7.2 (A), D8.2 (A), D9.2 (A), U6.2, U7.2, U8.2, U9.1 (VCC), U10.1 (VCC), U11.1 (VCC)
PhaseA: A1.11 (D8), R7.2, U9.2 (IN)
PhaseAOut: P1.1, R14.2, U12.1 (-)
PhaseASense: C3.2, R14.1, U3.2, U6.3, U9.6 (VS), U12.8 (+)
PhaseB: A1.12 (D9), R8.2, U10.2 (IN)
PhaseBOut: P1.2, R15.2, U13.1 (-)
PhaseBSense: C4.2, R15.1, U4.2, U7.3, U10.6 (VS), U13.8 (+)
PhaseC: A1.13 (D10/CS), R11.2, U11.2 (IN)
PhaseCOut: P1.3, R16.2, U14.1 (-)
PhaseCSense: C5.2, R16.1, U5.2, U8.3, U11.6 (VS), U14.8 (+)
Status1: A1.8 (D5), R4.1
Status2: A1.9 (D6), R5.1
Status3: A1.10 (D7), R6.1

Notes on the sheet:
Can handle 5-18V input
VCC decoupling and bootstrap capacitors should also be directly next to the gate driver ICs
Logic
MOSFET Gate Drivers
Output MOSFETs
We use PA2512FKF7W0R006E (C728340) resistors. 2 watts is enough as we should only be dissipating around 0.6 watts at full current with 0.006ohms It has a pretty rough ±1% tolerance, but... whatever. Better ones are like $10 each... The INA240A1D amplifier has a 20 V/V gain, so at 10 amps we modulat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
For my own reference lol V_out = V_in * R_2 / (R_1 + R_2) For 5V to 3.3V level shifting, R_2 / (R_1 + R_2) = 3.3 / 5, so e.g R_1 = 3.3k / R_2 = 2k
Status LEDs
Regulated outputs
DIR = LOW passes data B -> A
Level shifters (forced 5V to 3.3V)
Power input
Should handle ~10A hold current
Current sensing
Note: Gate resistors should be placed directly before the MOSFET gate pin to reduce PCB loop inductance

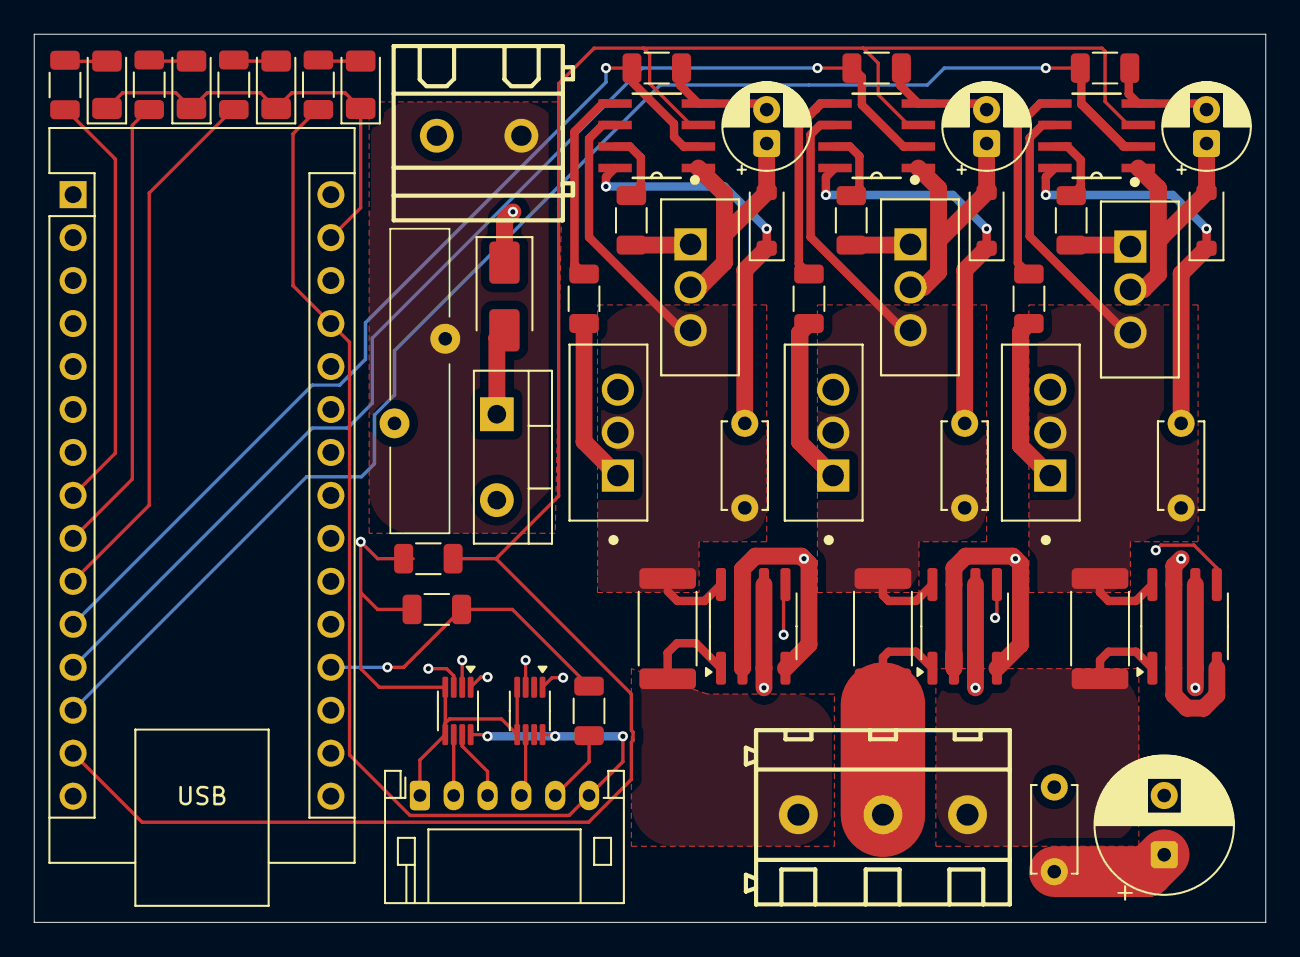
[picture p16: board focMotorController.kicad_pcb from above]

Board: 4 copper layers, 72.8 x 52.5 mm, 55 parts (0 on the bottom side), 50 nets.

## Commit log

2025-07-09 Initial empty project
    [focMotorController.kicad_pcb, focMotorController.kicad_sch]
2025-07-09 Start creating schematic
    Currently includes:
    - Power input circuitry and filtering
    - Logic: microcontroller and encoder connection
    - Level shifters for encoder
    - Status LEDs
    - Output MOSFETs
    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
    [STP55NF06L.step, STPS20L15D.step, TC4420EPA.step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]
2025-07-09 Add current sensing circuitry
    [focMotorController.kicad_sch]
2025-07-09 Finish initial routing
    [IR2104SPBF.step, focMotorController.kicad_pcb, focMotorController.kicad_sch]
2025-07-09 Compact PCB
    [focMotorController.kicad_pcb]
2025-07-09 Finish initial PCB version
    [focMotorController.kicad_pcb]
2025-07-10 Try to model motor with Python program (still a work-in-progress), set up PCB for JLCPCB
    [focMotorController-CuBottom.gbr, focMotorController-CuIn1.gbr, focMotorController-CuIn2.gbr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]
2025-07-10 Update schematics with remaining JLCPCB parts, finish BOM, and export manufacturing files
    [BOM-focMotorController.csv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]
2025-07-14 Clean up transformation and motor simulation code slightly, continue writeup
2025-07-15 Much better motor simulation, better graphing, and more documentation
2025-07-18 Add copper pours for high current traces and clean up PCB elsewhere
    [focMotorController.kicad_pcb]
2025-07-18 Fix small issues with copper pours and solder mask
    [focMotorController.kicad_pcb]
2025-07-18 Fix power plane contacting current sense
    [focMotorController.kicad_pcb]
